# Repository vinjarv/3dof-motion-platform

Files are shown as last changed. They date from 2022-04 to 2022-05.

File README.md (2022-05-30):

# 3dof-motion-platform

This project was a part of the subject AIS2102 Dynamical Systems at NTNU Ålesund, Spring 2022. The task given was to control the position of a ball on a platform. This included building the platform, designing a regulator, and implementing it in code.

## Folders:
- Code - Arduino and python code for running the project
- Code/playground - test code for various functions
- Matlab - files for generation regulator parameters and simulating the response
- Parts for 3D printing - STL files used in the project
- Parts for laser cutting - DXF files
- Starter code - supplied code examples from project 

## Python programs:
1.	Code/config_gui.py : GUI for selecting platform position and ball color mask
2.	Code/ball_control_servo_fast.py : Controls ball position on platform. Main project code

## Python setup / installation:

Navigate to folder and run in shell:
```console
cd Code
python -m venv venv
venv\Scripts\activate
python -m pip install --upgrade pip
pip install -r requirements.txt
```

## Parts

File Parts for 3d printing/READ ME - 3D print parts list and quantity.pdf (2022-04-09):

## Required 3D printed parts:

### 1. Servo Mounts – 3 pieces

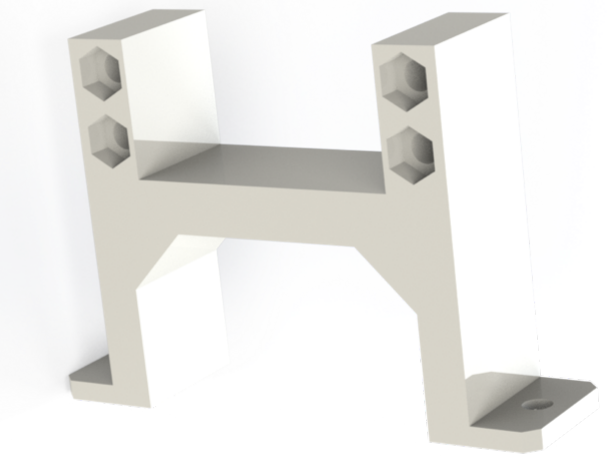
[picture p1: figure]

2. Servo horn – 3pieces

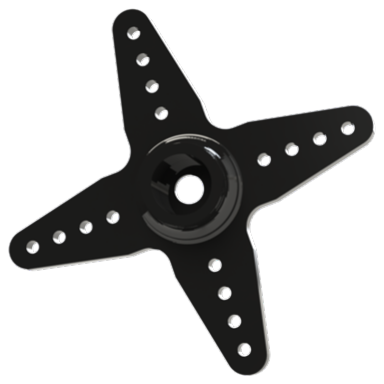
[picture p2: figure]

### 3. Servo horn adapter – 3 pieces

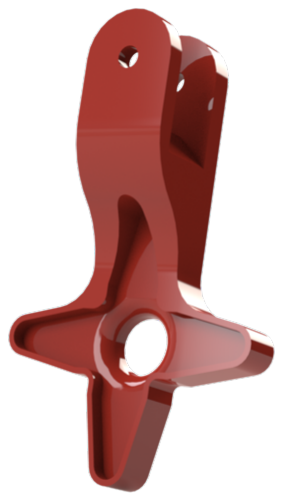
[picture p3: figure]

### 4. Tube ball end adapter – 3 pieces

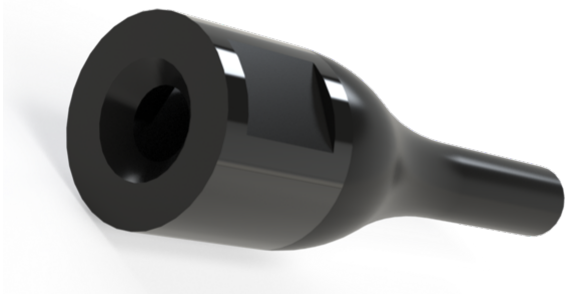
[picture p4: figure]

### 5. Magnet mount – 3 pieces

All the above shown parts are required to be 3D printed before the assembly.

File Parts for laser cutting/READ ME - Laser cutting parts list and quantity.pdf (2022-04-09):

## Required Laser Cutting parts:

### 1. Tabletop – 1 piece (Plywood)

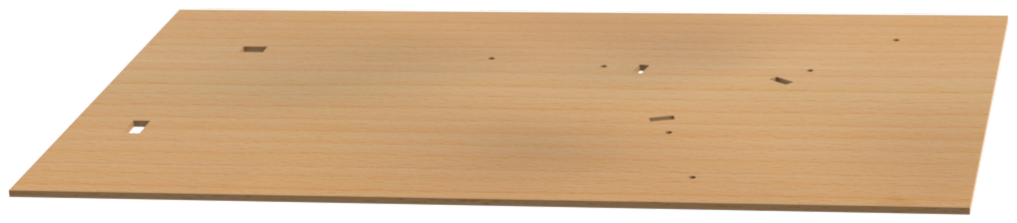
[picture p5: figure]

2. Top plate – 1 piece (Acrylic Glass – preferability spray painted black)

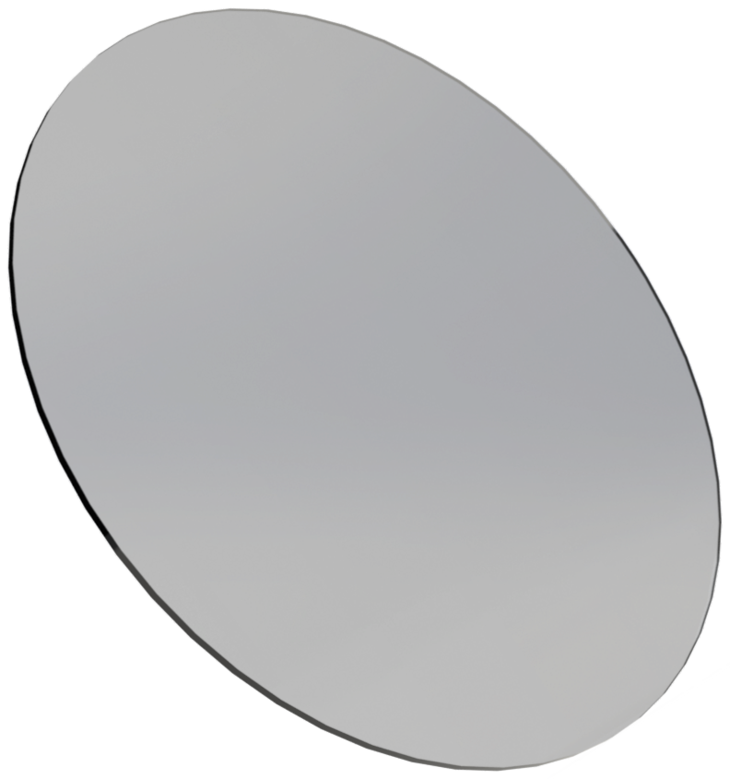
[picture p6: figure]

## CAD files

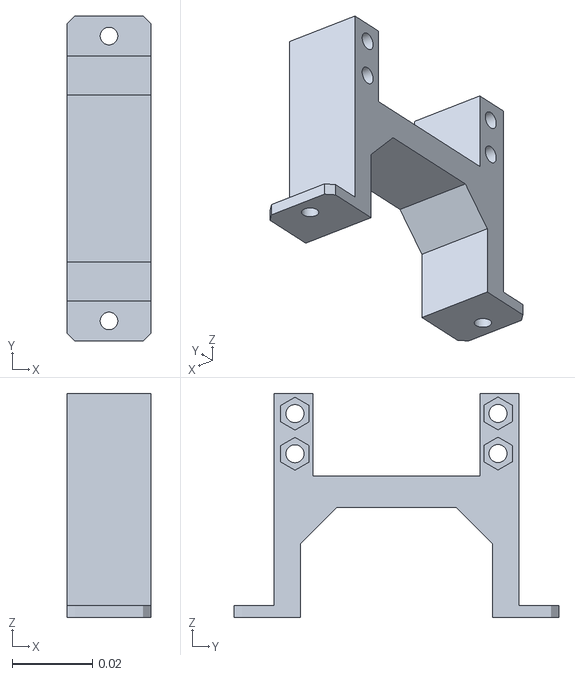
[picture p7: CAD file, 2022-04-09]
Parts for 3d printing/1. servo-mount.STL
0.021 x 0.081 x 0.0559

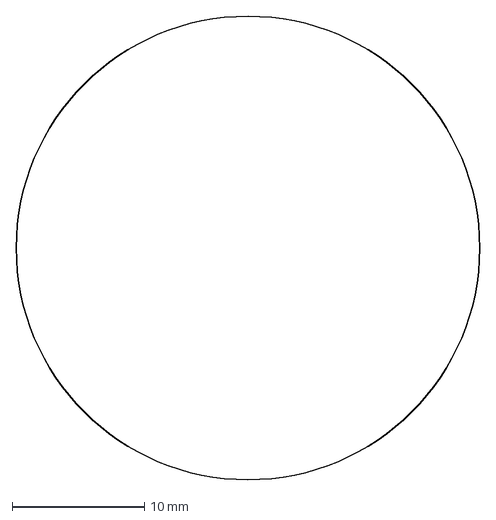
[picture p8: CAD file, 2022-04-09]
Parts for laser cutting/top_plate.DXF
35.0 x 35.0 mm

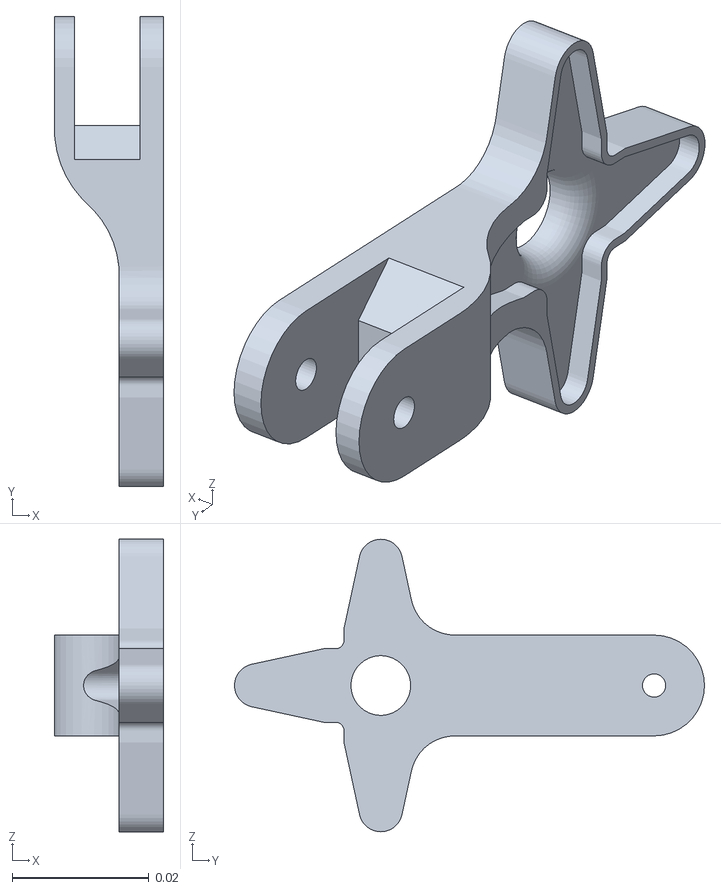
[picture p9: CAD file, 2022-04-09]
Parts for 3d printing/3. servo-horn-adapter.STL
0.016 x 0.0688 x 0.0429

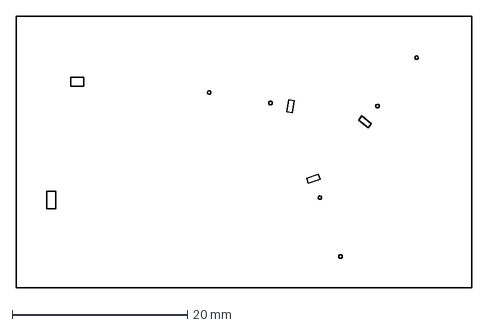
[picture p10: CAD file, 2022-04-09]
Parts for laser cutting/table_top.DXF
52.0 x 31.0 mm

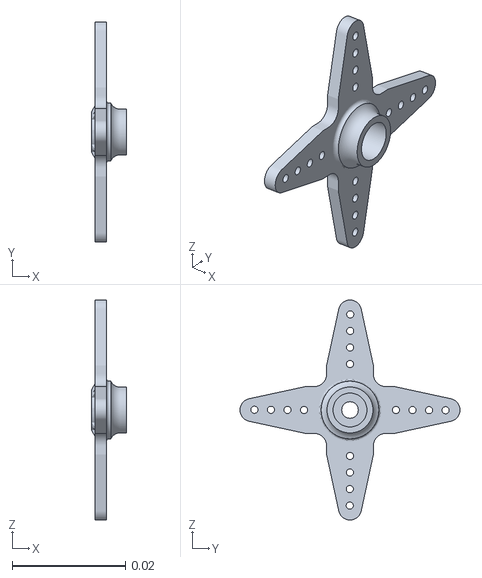
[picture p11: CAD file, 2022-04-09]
Parts for 3d printing/2. servo-horn.STL
0.00617 x 0.0388 x 0.0388

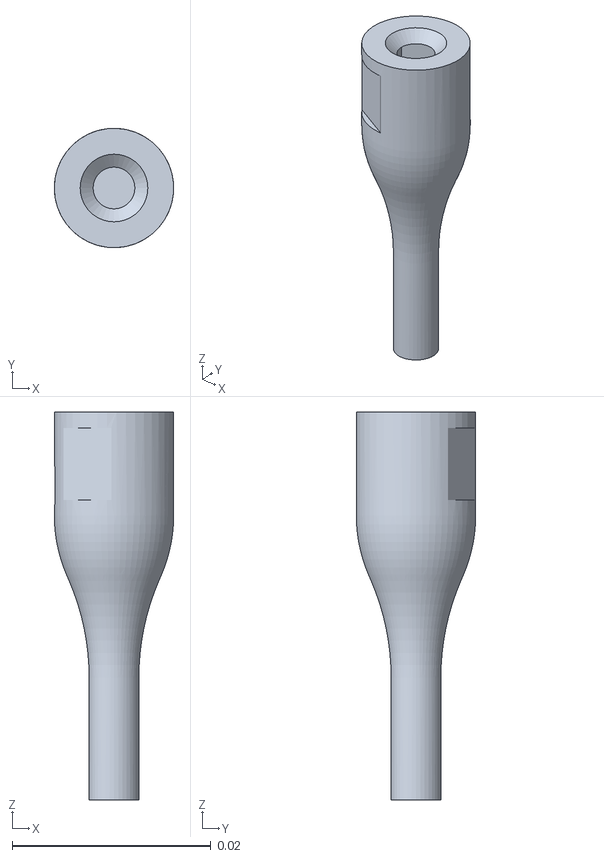
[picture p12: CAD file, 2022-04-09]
Parts for 3d printing/4. tube-ballend-adapter.STL
0.012 x 0.012 x 0.039

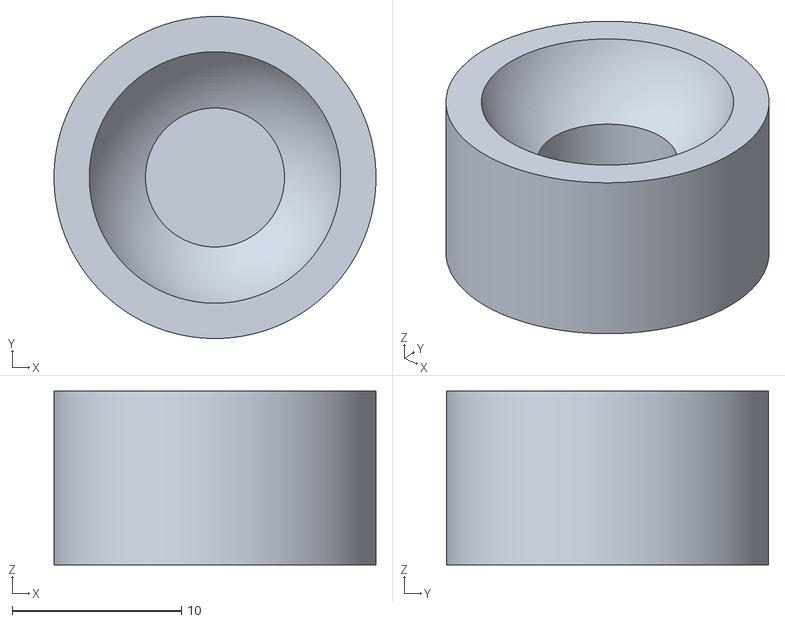
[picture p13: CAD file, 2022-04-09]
Parts for 3d printing/5. magnet-mount.stl
19.0 x 19.0 x 10.2

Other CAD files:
Parts for 3d printing/3d-print deler til plattform.f3d

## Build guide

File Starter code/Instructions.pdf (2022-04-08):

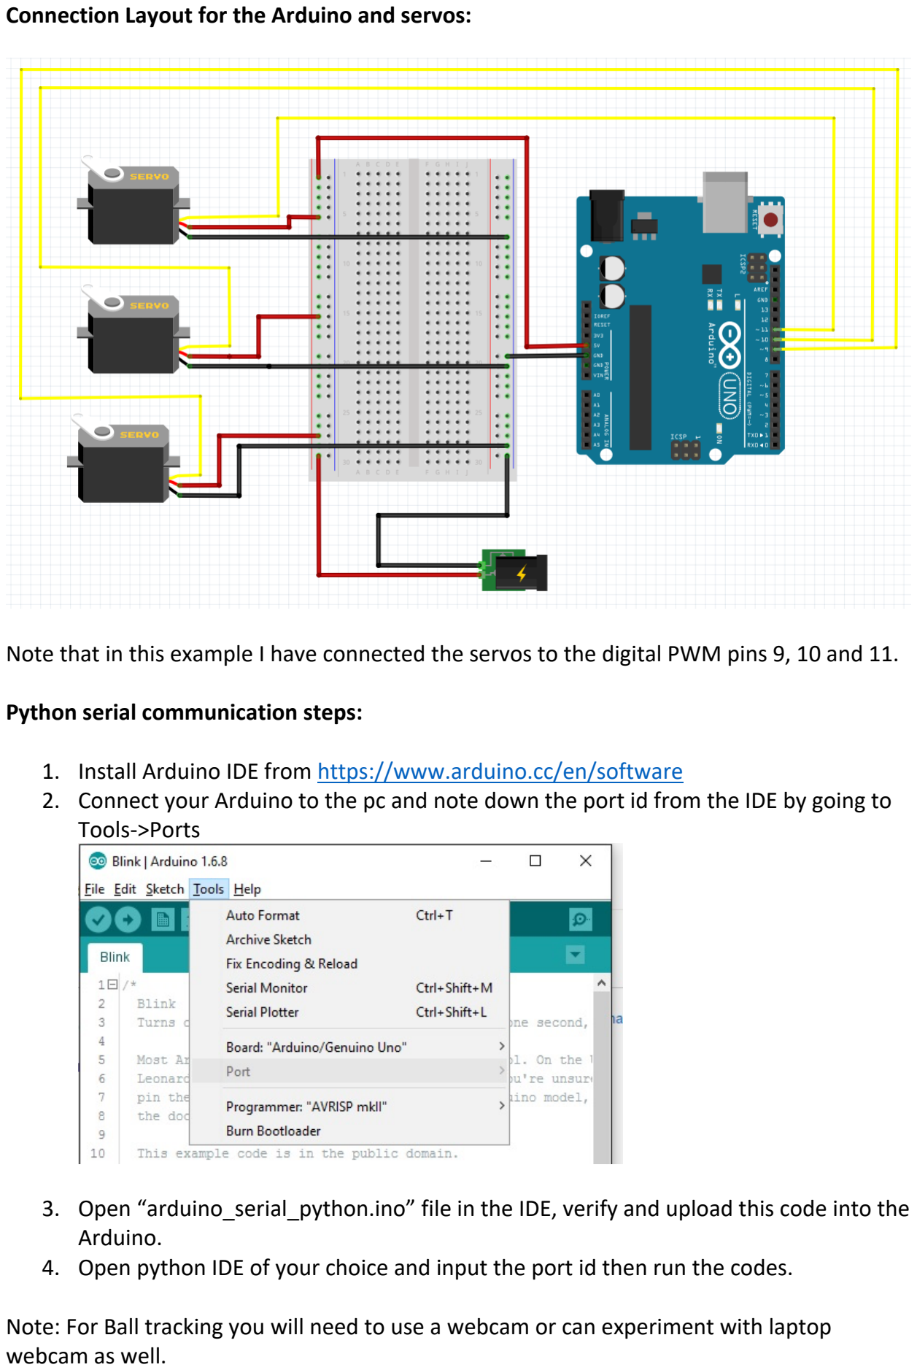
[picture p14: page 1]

Connection Layout for the Arduino and servos:

Note that in this example I have connected the servos to the digital PWM pins 9, 10 and 11.

Python serial communication steps:

1. Install Arduino IDE from https://www.arduino.cc/en/software
2. Connect your Arduino to the pc and note down the port id from the IDE by going to Tools->Ports
3. Open “arduino_serial_python.ino” file in the IDE, verify and upload this code into the Arduino.
4. Open python IDE of your choice and input the port id then run the codes.

Note: For Ball tracking you will need to use a webcam or can experiment with laptop webcam as well.

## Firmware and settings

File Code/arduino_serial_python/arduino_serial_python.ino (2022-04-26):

#include <Servo.h>    //modified from https://forum.arduino.cc/t/serial-input-basics-updated/382007/3

const byte numChars = 32;
char receivedChars[numChars];
char tempChars[numChars];   // temporary array for use when parsing

int servoPosArray[3];    // variables to hold the parsed data
boolean newData = false;

Servo servo1; //create the servo objects
Servo servo2;
Servo servo3;

const int home_pos[] = {90, 78, 85}; // Center position of servos


void setup() {
    Serial.begin(250000);
    Serial.println("This program expects 3 integers");
    Serial.println("Enter the angles formated like this (35, -12, 24)  ");
    Serial.println();
    Serial.setTimeout(100);

    servo1.attach(9);  //attach the servo objects to arduino pins
    servo2.attach(10);
    servo3.attach(11);
    servo1.write(home_pos[0]);   //set servos to centerposition
    servo2.write(home_pos[1]);
    servo3.write(home_pos[2]);
}

void loop() {
    recvWithStartEndMarkers();
    if (newData == true) {
        strcpy(tempChars, receivedChars);
            //this temporary copy is necessary to protect the original data
            //because strtok() used in parseData() replaces the commas with \0
        parseData();
        useParsedData();
        newData = false;
    }
}


/**
 * Reads serial data to a string
 * 
 * Data is read continously if a start marker is detected, then written to receivedChars.
 * Function returns when the end marker is read.
 */
void recvWithStartEndMarkers() {
    static boolean recvInProgress = false;
    static byte ndx = 0;
    char startMarker = '(';
    char endMarker = ')';
    char rc;

    while (Serial.available() > 0 && newData == false) {
        rc = Serial.read();

        if (recvInProgress == true) {
            if (rc != endMarker) {
                receivedChars[ndx] = rc;
                ndx++;
                if (ndx >= numChars) {
                    ndx = numChars - 1;
                }
            }
            else {
                receivedChars[ndx] = '\0'; // terminate the string
                recvInProgress = false;
                ndx = 0;
                newData = true;
            }
        }

        else if (rc == startMarker) {
            recvInProgress = true;
        }
    }
}

/**
 * Split serial data into 3 integers
 * 
 * Data is written to servoPosArray
 */
void parseData() {

    char * strtokIndx; //this is used by strtok() as an index

    strtokIndx = strtok(tempChars,","); //get the first value from the Serial-string 
    servoPosArray[0] = atoi(strtokIndx); //copy it to the positionarray
 
    strtokIndx = strtok(NULL, ","); //this continues where the previous call left off
    servoPosArray[1] = atoi(strtokIndx); //adds 2nd value to positionarray

    strtokIndx = strtok(NULL, ",");
    servoPosArray[2] = atoi(strtokIndx); //adds 3rd value to positionarray
}

/**
 * Sets angles of servo motors to the values in servoPosArray
 */
void useParsedData() {
    servo1.write(servoPosArray[0] + home_pos[0]);
    servo2.write(servoPosArray[1] + home_pos[1]);
    servo3.write(servoPosArray[2] + home_pos[2]);
}

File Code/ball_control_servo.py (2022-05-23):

from multiprocessing import Queue, Process
import threading
import cvzone
import cv2
import serial
import time
import tkinter as tk
from PIL import Image, ImageTk
import numpy as np
from numpy import pi, cos, sin, arcsin, sqrt
import configparser


# ------------------------------------------- Ball tracking and position control -------------------------------------------
"""
Run regulator, camera capture and GUI in parallel 
"""

# Serial/arduino setup
port_id = 'COM5'

# Define servo angles and set a value
servo1_angle = 0
servo2_angle = 0
servo3_angle = 0

# Maximum allowable rotation angle for the servos
servo_angle_limit = [[ -90, 90 ],   # Servo 1
                     [ -90, 90 ],   # Servo 2
                     [ -90, 90 ]]   # Servo 3

# Camera
cap_id = 1
IMG_W = 1280
IMG_H = 720

x, y = 0, 0 # Mouse click event coords
plat_c, plat_r = [0,0], 0 # Platform definition
col_mask = {'hmin': 0, 'smin': 0, 'vmin': 0, 'hmax': 255, 'smax': 255, 'vmax': 255}

plat_actual_r = 0.175 # Actual radius in m

# Regulator parameters
reg_b = [4.8521423282,0.1963758629,-4.6557664653]
reg_a = [1.0000000000,-0.5030443975,0.1419604340]

# Config file handling
config_file = configparser.ConfigParser()
config_file.read("config.ini")

def save_configfile():
    global config_file, plat_c, plat_r, col_mask
    with open("config.ini","w") as file_object:
        for key in col_mask:
            config_file["ColMask"][key] = str(col_mask[key])
        config_file["Platform"]["plat_c_x"] = str(plat_c[0])
        config_file["Platform"]["plat_c_y"] = str(plat_c[1])
        config_file["Platform"]["plat_r"] = str(plat_r)
        config_file.write(file_object)

def read_configfile():
    global config_file, plat_c, plat_r, col_mask
    for key in col_mask:
        col_mask[key] = int(config_file["ColMask"][key])
    plat_c[0] = float(config_file["Platform"]["plat_c_x"])
    plat_c[1] = float(config_file["Platform"]["plat_c_y"])
    plat_r = float(config_file["Platform"]["plat_r"])
    time.sleep(0.1)
    print("Settings loaded from config.ini")

def find_ball(img, col_mask):
    # Mask image and return the position and area of the largest contour
    mask, masked_image = mask_img(img, col_mask)
    img_contour, contours = cvzone.findContours(img, mask)
    ball_pos_abs = (0,0)
    ball_area = 0
    img_contour = None
    if contours:
        # Ball found 
        ball_pos_abs = ((contours[0]['center'][0]), (contours[0]['center'][1]))
        ball_area = contours[0]['area']
    return ball_pos_abs, ball_area, img_contour 

def mask_img(img, col_mask):
    # Remove pixels outside mask range
    hsv = cv2.cvtColor(img, cv2.COLOR_BGR2HSV)
    min = np.array([col_mask["hmin"], col_mask["smin"], col_mask["vmin"]])
    max = np.array([col_mask["hmax"], col_mask["smax"], col_mask["vmax"]])
    mask = cv2.inRange(hsv, min, max)
    global platform_mask
    mask = cv2.bitwise_and(mask, platform_mask)
    res = cv2.bitwise_and(img, img, mask=mask)
    return mask, res

class FreshestFrame(threading.Thread):
    # From https://gist.github.com/crackwitz/15c3910f243a42dcd9d4a40fcdb24e40
	def __init__(self, capture, name='FreshestFrame'):
		self.capture = capture
		assert self.capture.isOpened()

		# this lets the read() method block until there's a new frame
		self.cond = threading.Condition()

		# this allows us to stop the thread gracefully
		self.running = False

		# keeping the newest frame around
		self.frame = None

		# passing a sequence number allows read() to NOT block
		# if the currently available one is exactly the one you ask for
		self.latestnum = 0

		# this is just for demo purposes		
		self.callback = None
		
		super().__init__(name=name)
		self.start()

	def start(self):
		self.running = True
		super().start()

	def release(self, timeout=None):
		self.running = False
		self.join(timeout=timeout)
		self.capture.release()

	def run(self):
		counter = 0
		while self.running:
			# block for fresh frame
			(rv, img) = self.capture.read()
			assert rv
			counter += 1

			# publish the frame
			with self.cond: # lock the condition for this operation
				self.frame = img if rv else None
				self.latestnum = counter
				self.cond.notify_all()

			if self.callback:
				self.callback(img)

	def read(self, wait=True, seqnumber=None, timeout=None):
		# with no arguments (wait=True), it always blocks for a fresh frame
		# with wait=False it returns the current frame immediately (polling)
		# with a seqnumber, it blocks until that frame is available (or no wait at all)
		# with timeout argument, may return an earlier frame;
		#   may even be (0,None) if nothing received yet

		with self.cond:
			if wait:
				if seqnumber is None:
					seqnumber = self.latestnum+1
				if seqnumber < 1:
					seqnumber = 1
				
				rv = self.cond.wait_for(lambda: self.latestnum >= seqnumber, timeout=timeout)
				if not rv:
					return (self.latestnum, self.frame)

			return (self.latestnum, self.frame)

class CameraHandler(Process):
    def __init__(self, cap_id, queues):
        self.cap_id = cap_id
        self.queues = queues
        super(CameraHandler, self).__init__(target=self.loop)

    def loop(self):
        print("Starting CameraHandler loop")
        self.cap = cv2.VideoCapture(cap_id, cv2.CAP_DSHOW)
        self.cap.set(cv2.CAP_PROP_FRAME_WIDTH, IMG_W)
        self.cap.set(cv2.CAP_PROP_FRAME_HEIGHT, IMG_H)
        self.cap.set(cv2.CAP_PROP_FPS, 30)
        self.cap.set(cv2.CAP_PROP_FOURCC, cv2.VideoWriter_fourcc('M', 'J', 'P', 'G'))
        self.cap.set(cv2.CAP_PROP_EXPOSURE, -8)
        self.cap.set(cv2.CAP_PROP_BUFFERSIZE, 0)
        self.fresh = FreshestFrame(self.cap)
        # Will try to keep queues full with new frames
        while True:
            retval, img  = self.fresh.read()
            if retval:
                for q in self.queues:
                    if q.qsize() == 0:
                        q.put_nowait(img)
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

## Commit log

2022-04-09 Added 3d files for printing and laser cutting
    [1. servo-mount.STL, 2. servo-horn.STL, 3. servo-horn-adapter.STL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]
2022-04-30 Added updated Windows code to fix issues with serial port
    [ball_crontol_servo_win.py, two_in_one_win.py]
2022-05-16 Read camera in separate process
2022-05-19 Fixed y rotation matrix
    [roll_pitch_control.py]
2022-05-19 GUI-less version of code, should have less jitter
    [ball_control_servo_fast.py]
2022-05-19 Almost working version, jittery
    [ball_control_servo.py]
